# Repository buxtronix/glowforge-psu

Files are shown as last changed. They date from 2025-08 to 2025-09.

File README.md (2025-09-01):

# Documenting the Glowforge Power Supply

This repository aims to contain a collection of information on the
power supply within the Glowforge Pro.

These power supplies frequently fail, and there is little documentation
that can assist when trying to repair them.

[Scott Wiederhold](https://community.openglow.org/u/scottw514/summary) has
done a remarkable job at trying to reverse engineer the GF in order to
produce an Open Source replacement controller and his
[OpenGlow forum](http://community.openglow.org/) contains a lot of
photos, teardowns and information.

I have been trying to repair a broken power supply myself, and wanted
to combine a bunch of information from various posts, as well as what
myself and others found.

> [!TIP]
> Please contribute here if you can. Any additional or improved
> information will be greatly appreciated by many.

> [!CAUTION]
> This information involves working with lethal voltages (400-22,000 volts)
> and high power laser radiation!
> It is intended only for people who are sufficiently experienced in
> working with high voltage electronics and understand the necessary
> precautions.

> [!WARNING]
> The information contained here is provided on a "best effort" basis
> and is not guaranteed to be accurate. Consider this information to
> be a starting point where you should then use your best judgement
> and double checks before relying on anything.

## References

Some links to relevant information, mostly on OpenGlow:

 * [Teardown of power components](https://community.openglow.org/t/reverse-engineering-pr0n/242/2)
 * [High voltage troubleshooting](https://community.openglow.org/t/laser-not-firing/680/2)
 * [Testing HV output](https://community.openglow.org/t/gf-not-fire-working-process/847/2)
 * [Analysis/photos of GF boards](https://community.openglow.org/t/list-of-ics-on-the-control-board/988)
 * [OpenGlow schematic](https://community.openglow.org/t/openglow-prototype-2-schematics/255)

## Extracting the supply

The power supply is quite difficult to get out, as it wedged into a tight
corner and attached using cables with very little slack.

Ken S has made [two](https://www.youtube.com/watch?v=dVIbavUEy1M)
[videos](https://www.youtube.com/watch?v=0B0-IHG0M_s) of the removal
process which is very involved and will probably take an hour.
At one point the machine is flipped upside down - take great care
to ensure the gantry is secure as you dont want it crashing to
one side during the flip.

## Basic information.

A lot of basic teardown information can be found in
[this post](https://community.openglow.org/t/reverse-engineering-pr0n/242)
from Scott.

The power supply is a custom unit which provides several voltages
required by the machine:

 * 3.3v for logic and control board.
 * 12v for various accessories (pump, fans, motors, etc)
 * 40v for higher power components (more fans, peltier perhaps?)
 * 12-22kV for the laser tube.

It also has some control signals which communicate over the ribbon
cable. The 12v, 40v, and HV outputs are only enabled when the right
control signals are set.

It's possible to control the PSU when outside the machine, per
[this post](https://community.openglow.org/t/gf-not-fire-working-process/847/2)

## Opening the PSU

Remove the screws attaching the top lid (where the ribbon cable and HV red
wire are).

Remove the panel on the side by undoing the 4 screws holding it on.

In that panel you can access two cable bundles between the top and bottom
boards. Unplug these from the bottom board.

Remove the top cover and attached board. Take care with the red and white
wires. The red HV wire has a grommet that splits apart when the cable tie
is removed.

The top board is screwed into the lid with 8 Phillips head screws. You will
need to use a driver with a thin shaft to remove the center one as there
is not much space. Be careful not to damage or crack the core of the
flyback transformer.

## Connectors

These are the connectors on the PSU. You could create extension cables in order
to run the machine with the PSU outside of it for testing.

__Molex mini-fit jr 6-way__ is the large 6-pin connector to the daughterboard [Digikey link](https://www.digikey.com/en/products/detail/molex/0766500076/2115933)
  
__TE Connectivity Economy 2.5 4 way__ is the smaller one next to it [Digikey link](https://www.digikey.com/en/products/detail/te-connectivity-amp-connectors/1744417-4/4730270) [mating connector](https://www.digikey.com/en/products/detail/te-connectivity-amp-connectors/1969588-4/5021426)

__Molex 30-way 1mm ribbon cable__ note top on on side bottom on the other [Digikey link](https://www.digikey.com/en/products/detail/molex/0152670468/4427333)

This is the pinout of the ribbon cable:

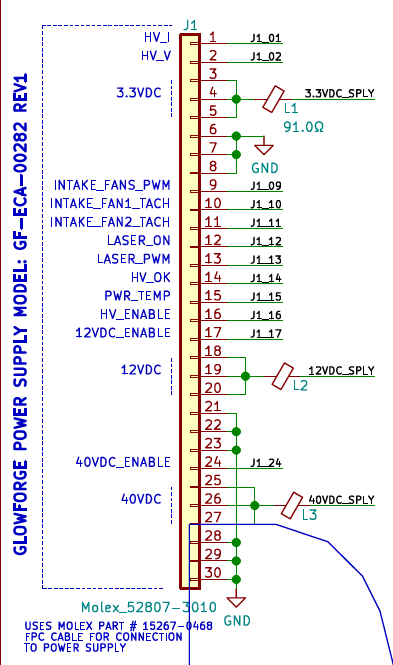
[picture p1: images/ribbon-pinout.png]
Ribbon cable pinout


## Common failure modes

### Red wire

The long red wire carries the high voltage to the laser tube. This
is a common cause of laser failures, with the insulation failing
and the power arcing through to the gantry earth.

There is loads of information online, just search for "glowforge red wire".

### Flyback transformer failure

The high voltage transformer can fail. It seems a common failure mode is
for the components in the potted section to burn out. The currently only
know fix for this is to replace the transformer from a donor unit (the
transformer is a custom unit and cannot be purchased separately).

It *might* be possible to repair the failed parts, but it is risky and
would require cutting the parts out of the potting , replacing them,
and re-potting it. A vacuum chamber would be needed at minimum to
remove air bubbles which would otherwise enable arc-over internally.

### HV supervisor failure

[TODO]

### Low voltage failures

[TODO]

## HV circuit description

TODO: Describe HV principle, operation and parts.

The driver daughterboard has some reverse engineering attempts
documented [here](hv-supervisor/)

## HV circuit troubleshooting

## Testing the supply

### Powerup testing

Using an appropriate dummy load and sending the right control signals,
the various outputs on the supply can be enabled for testing.

Scott has [a post](https://community.openglow.org/t/gf-not-fire-working-process/847/2)
covering this procedure.

Setting the various signals on the ribbon cable can be tricky. I designed a
breakout board which brings these connections into a regular header socket,
and also acts as a passthrough to the control board for verify operation
when installed.

Designs and Gerbers are [available here](breakout-pcb/).

### Flyback ring test

The secondary windings on the flyback can become shorted. This will result
in no or very weak output to the tube, and potential failure of the output
Mosfets.

It's possible to test for such a short with a ring test. A ring test works
by applying a weak square wave to a resonant circuit around the flyback core.
On a good flyback, the circuit will "ring" and oscillate with a gradual
dampening. If there is a shorted turn, this will absorb all the energy
and the ring will diminish rapidly, much like a ringing bell being touched.

This test can be easily done using just a scope, a capacitor (~0.5-2uF), and
a length of thin wire. It's not necessary to remove the flyback from the
PCB.

The diagram below shows the testing setup. It consists of:

 * A scope with a signal output, 1kHz at 1 volt (often the "cal" output)
 * A capacitor (non-polarised, ideally film) of between 0.5 and 2uF
 * 4-5 turns of insulated wire around the core. Thin, as there's not much space.
 * Connect it all in parallel - the flyback does not need to be removed from the PCB
 * Set the scope timebase to 200uS/div, and the vertical to around 2-10mV/div

A flyback with no shorted turns will look something like the left picture,
whereas if it looks more like the right picture, its almost certainly got
shorted turns and the flyback will need replacing.

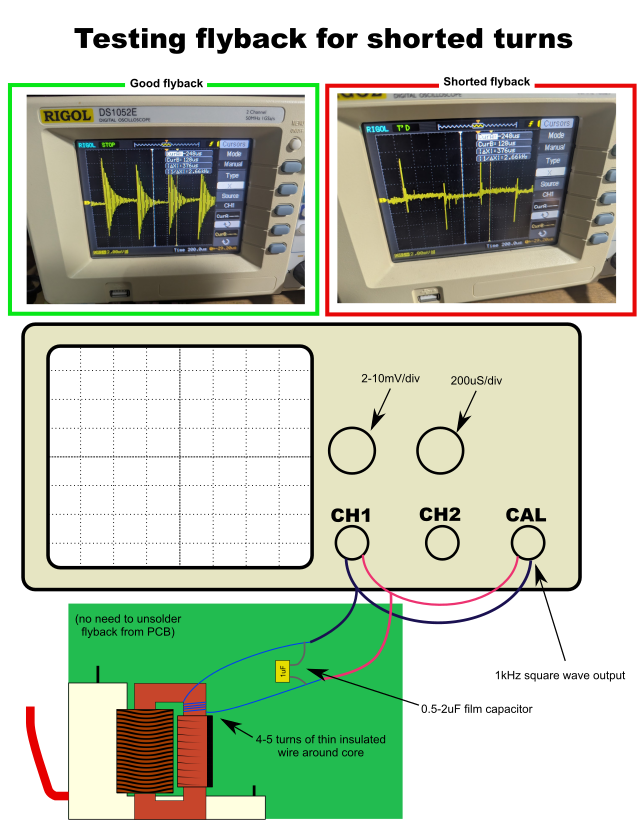
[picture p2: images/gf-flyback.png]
Flyback test setup


TODO: Add info on extending cables outside the GF machine.

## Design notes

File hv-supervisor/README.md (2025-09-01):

# HV supervisor board

This contains a work-in-progress reverse-engineered schematic of the HV supervisor
daughterboard. This is shown in
[this post](https://community.openglow.org/t/reverse-engineering-pr0n/242/2).

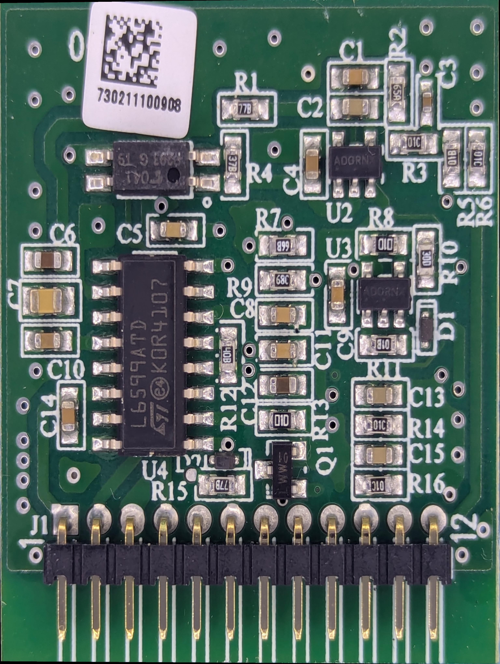
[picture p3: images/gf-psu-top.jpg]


The SOT23-5 chips are likely opamps or comparators, possibly LMC7101 or TLV7211. This is
based upon their likely function and likely pinouts. The markings don't show up on
any known database.

The main chip, an [LT6599ATD](https://www.st.com/resource/en/datasheet/l6599.pdf)
is a fairly common switchmode controller. A detailed
[reference design](https://www.mouser.com/catalog/specsheets/eval6599-90w.pdf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) is also available.

The optocoupler is likely a [TLP293](https://toshiba.semicon-storage.com/info/TLP293_datasheet_en_20191129.pdf?did=14419&prodName=TLP293).

## Pinout

This has been reverse engineered from information such as the schematic (below),
the L6599AT datasheet, 30-pin ribbon cable pinout, and various measurements.

| Pin  | Name | Description |
|---|---|---|
| 1 | OUT | This connects to the half-bridge leg, linking the two driver MOSFETs |
| 2 | HVG | The gate drive for the high side MOSFET of the half-bridge |
| 3 | GND | Ground |
| 4 | VCC | +12V supply for this board. |
| 5 | LVG | The gate drive for the low side MOSFET of the half-bridge |
| 6 |  LASER_ON  | Links to `LASER_ON` on the 30-pin ribbon. The last signal for enabling the HV |
| 7 | HV_OK | Goes low if the HV driver chip shuts off the HV. Connects to PFC_STOP of the L6599AT |
| 8 | DIS | Connects to the DIS pin of the L6599AT. Disables the chip if it is set high |
| 9 | I_SEN | Primary current sense, connects to the main sense resistors on the MOSFET low side. |
| 10 | LASER_PWM  | Links to `LASER_PWM` on the 30-pin ribbon. Used to PWM the laser for lower power cuts |
| 11 | LINE | Connects to LINE on the LA6599AT.<br/>Used for brownout detection, this senses the 60v rail is ok via a divider |
| 12 | HV_I | Tube current detection. Connects to a current sense on the HV return |

Typical signals that would be expected on these pins (also educated guesses):

| Pin  | Signal |
|---|---|
| 1 | ~60v sine wave, this is the full primary voltage.
| 2 | 12V square wave ~30KHz to drive the high side mosfet gate. |
| 3 | 0v ground |
| 4 | 12VDC as this is a stable supply voltage for this board. |
| 5 | 12V square wave ~30KHz to drive the low side mosfet gate |
| 6 | 3.3v should be applied here to turn on the HV output. |
| 7 | This should be around 1.8v (pulled high) if the chip is running |
| 8 | Should be 0v. At around 1.75v it will shutdown the chip |
| 9 | Will track the MOSFET current through the sense resistors. From 0.8v it will reduce drive, and shut off completely at 1.5v |
| 10 | PWM signal (at 3.3v) to modulate the output. Can be a DC signal for full power. 0v will disable the HV |
| 11 | Detects under and overvolt of the supply voltage. The L6599AT will shutoff with undervoltage if this is < 1.24v, and overvoltage shutoff if > 6v. This is connected via a divider to the +60v rail, also seems to be linked to `LASER_ON` on the main board. |
| 12 | Value range is unknown, but likely is proportional to the tube current measured on the HV return. Connects to an optocoupler on the STBY line of the L6599AT in similar fashion to the datasheet description, typically to regulate the output |

## Testing

The board should be independently testable, as all of the functions are
now known. Testing involves setting some voltages on various pins and
monitoring on a scope for the gate drive signals.

**The below connections may cause a failure of the driver as the correct
wiring for pin 1 is not yet known (leaving the chip OUT pin unconnected
might be problematic).** Verification TBD

| Pin  | What to connect/measure.
|---|---|
| 1 |  |
| 2 | Should be a ~30KHz square wave |
| 3 | Connect to ground |
| 4 | Connect to +12VDC |
| 5 | Should be a ~30KHz square wave out of phase with pin 2 |
| 6 | Connect this to a 3.3v source, enables the driver |
| 7 | Leave floating |
| 8 | Connect to ground. |
| 9 | Connect to ground. |
| 10 | Connect to 3.3v, PWM input |
| 11 | Connect to 3.3v to keep the brown out detector happy |
| 12 | Leave floating |

The following shows a test setup I have used with success. When measuring
the gates of both Mosfets, you will see each has a square wave out of phase
with the other. The frequency will be around 30-32KHz with a magnitude of
~24v on the high side Mosfet, and ~12v on the low side.

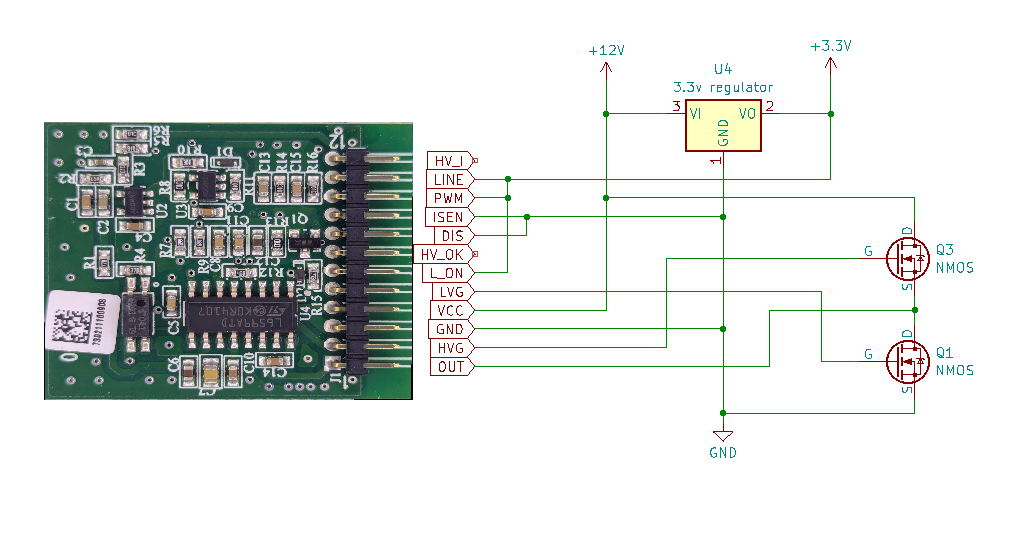
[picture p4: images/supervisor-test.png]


## Schematic

[This](glowforge-psu-hvbrd.pdf) has been reverse engineered from photos and measurements of the board. It's drawn in
Kicad and all files are here.

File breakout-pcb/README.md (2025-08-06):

# Breakout board for Glowforge power supply

A board to assist with testing and troubleshooting of a Glowforge
Pro power supply.

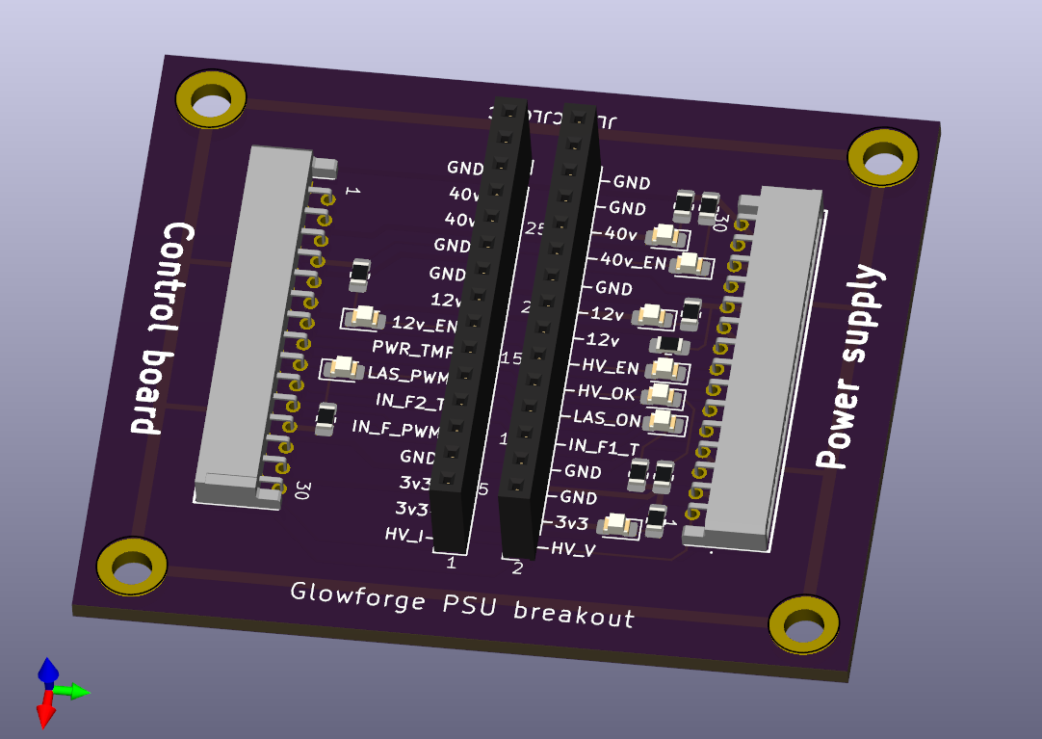
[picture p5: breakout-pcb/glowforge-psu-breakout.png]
Kicad render of breakout


Features:

- All 30 pins have passthrough and breakout to 0.1" headers.
- Can be used one-sided for testing standalone
- Can be used inline to monitor a connected supply.
- LEDs to monitor some signals

The gerbers.zip file can be uploaded to most board houses directly for
ordering. e.g for [JLCPCB](http://jlcpcb.com) upload to the 'Instant Quote'
form on their homepage, you can select the default options, order, and
have 5 boards delivered for around $USD5.

The boards will require the following additional parts:

 - 2 x Molex 52807-3010 connectors
 - 2 x 15-pin standard header sockets
 - 9 x 0805 SMD resistors
   - 1 x 8.2k
   - 1 x 2.2k
   - 7 * 270r
 - 9 x 0805 SMD LEDs

You may also need ribbon cable(s). The existing short one works to
connect to this breakout, but if you need a longer one or want to
extend, you need one with the following specs:

 - FPC cable
 - 1mm pitch
 - 30 way
 - OEM is Molex 15167 series

Note that they come in two flavours - either contacts on the same side at
both ends, or one end at the top and the other at the bottom. Between the
supply and control board as included it has the alternating one -- the
contacts on the PSU are on the bottom of the ribbon, and the contacts on
the control board are the top of the ribbon.

[Digikey link to original 50mm length](https://www.digikey.com.au/en/products/detail/molex/0151670467/3281720)

If you use this breakout as a passthrough, you will want
the variant with contacts on the same side to go to the control board.
[Digikey link to 100mm length](https://www.digikey.com.au/en/products/detail/molex/0151670471/3281724)

Longer lengths should also work and means you may be able to run the machine
with the supply outside it.

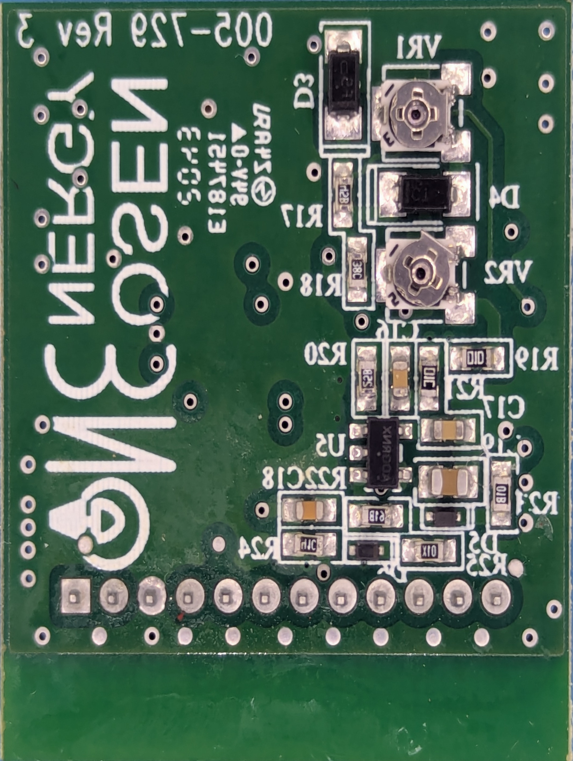
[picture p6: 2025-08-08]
images/gf-psu-bot.jpg

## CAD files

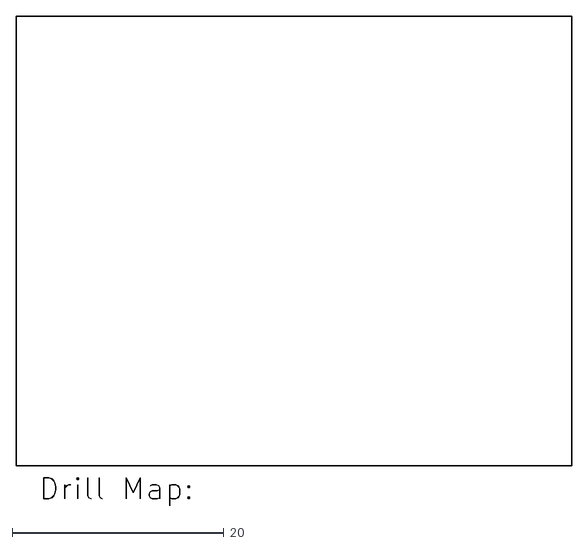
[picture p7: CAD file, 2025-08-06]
breakout-pcb/gerber/glowforge-psu-breakout-NPTH-drl_map.dxf
52.5 x 46.3

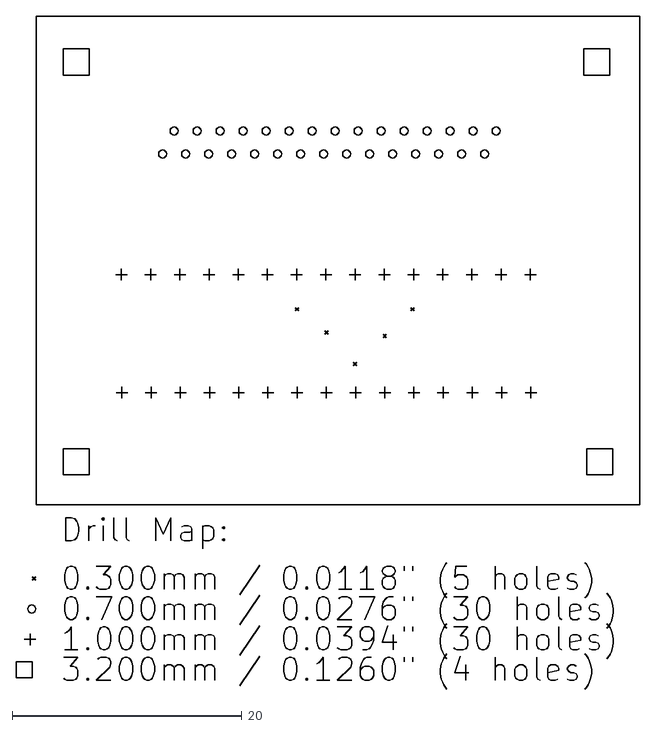
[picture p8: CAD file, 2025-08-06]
breakout-pcb/gerber/glowforge-psu-breakout-PTH-drl_map.dxf
54.2 x 58.5

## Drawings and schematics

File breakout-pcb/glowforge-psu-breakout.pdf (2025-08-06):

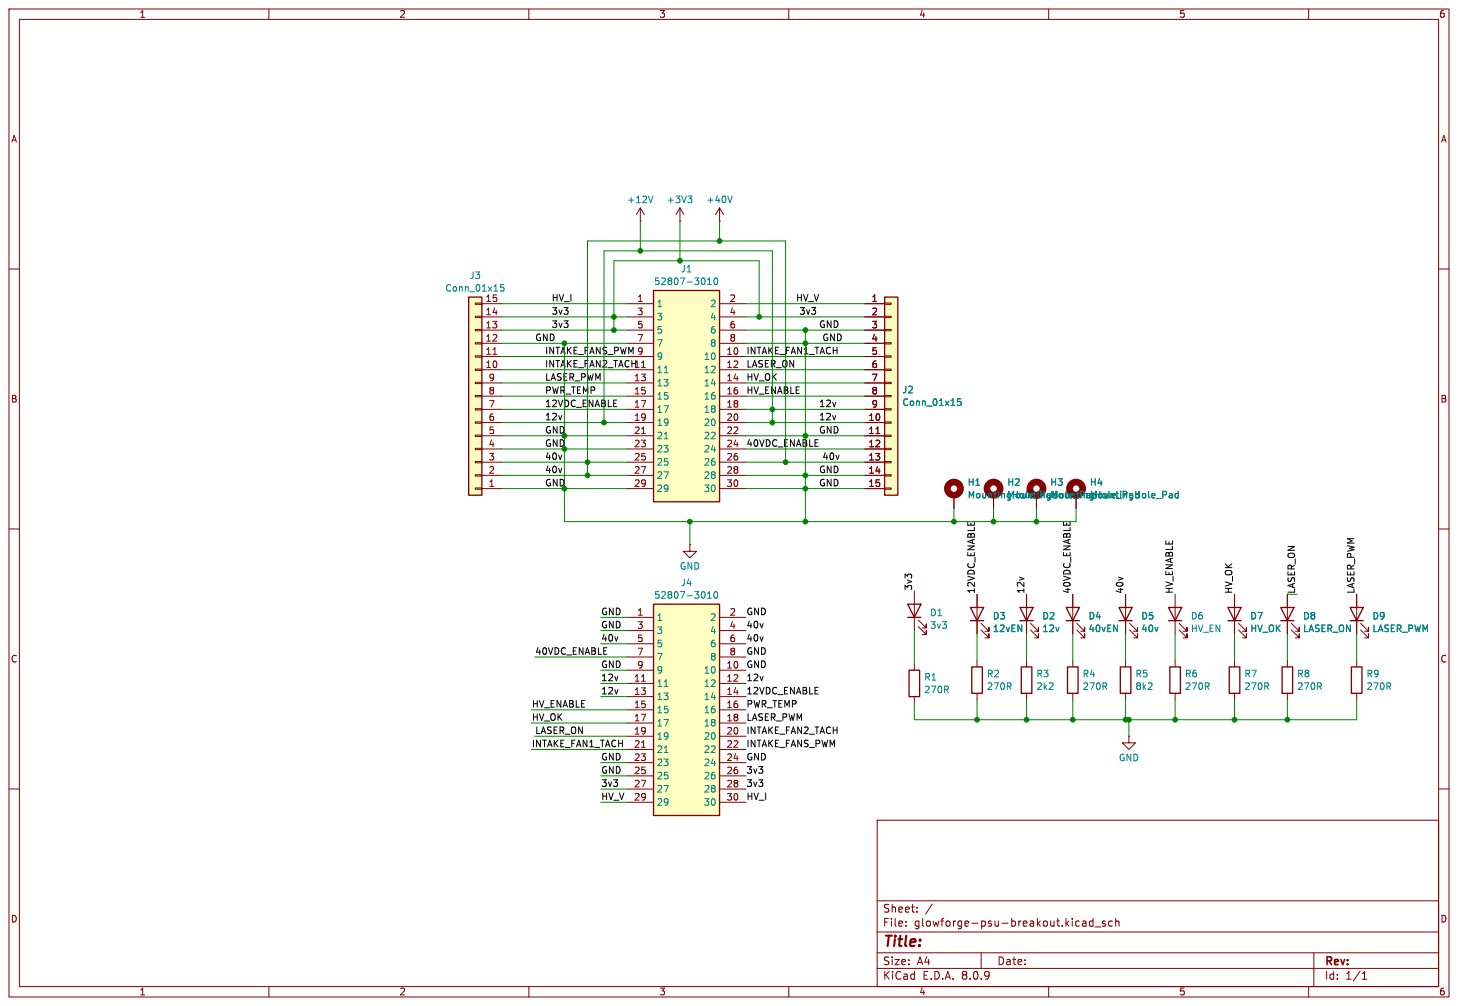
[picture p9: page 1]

Id: 1/1 Title: File: glowforge-psu-breakout.kicad_sch Sheet: /

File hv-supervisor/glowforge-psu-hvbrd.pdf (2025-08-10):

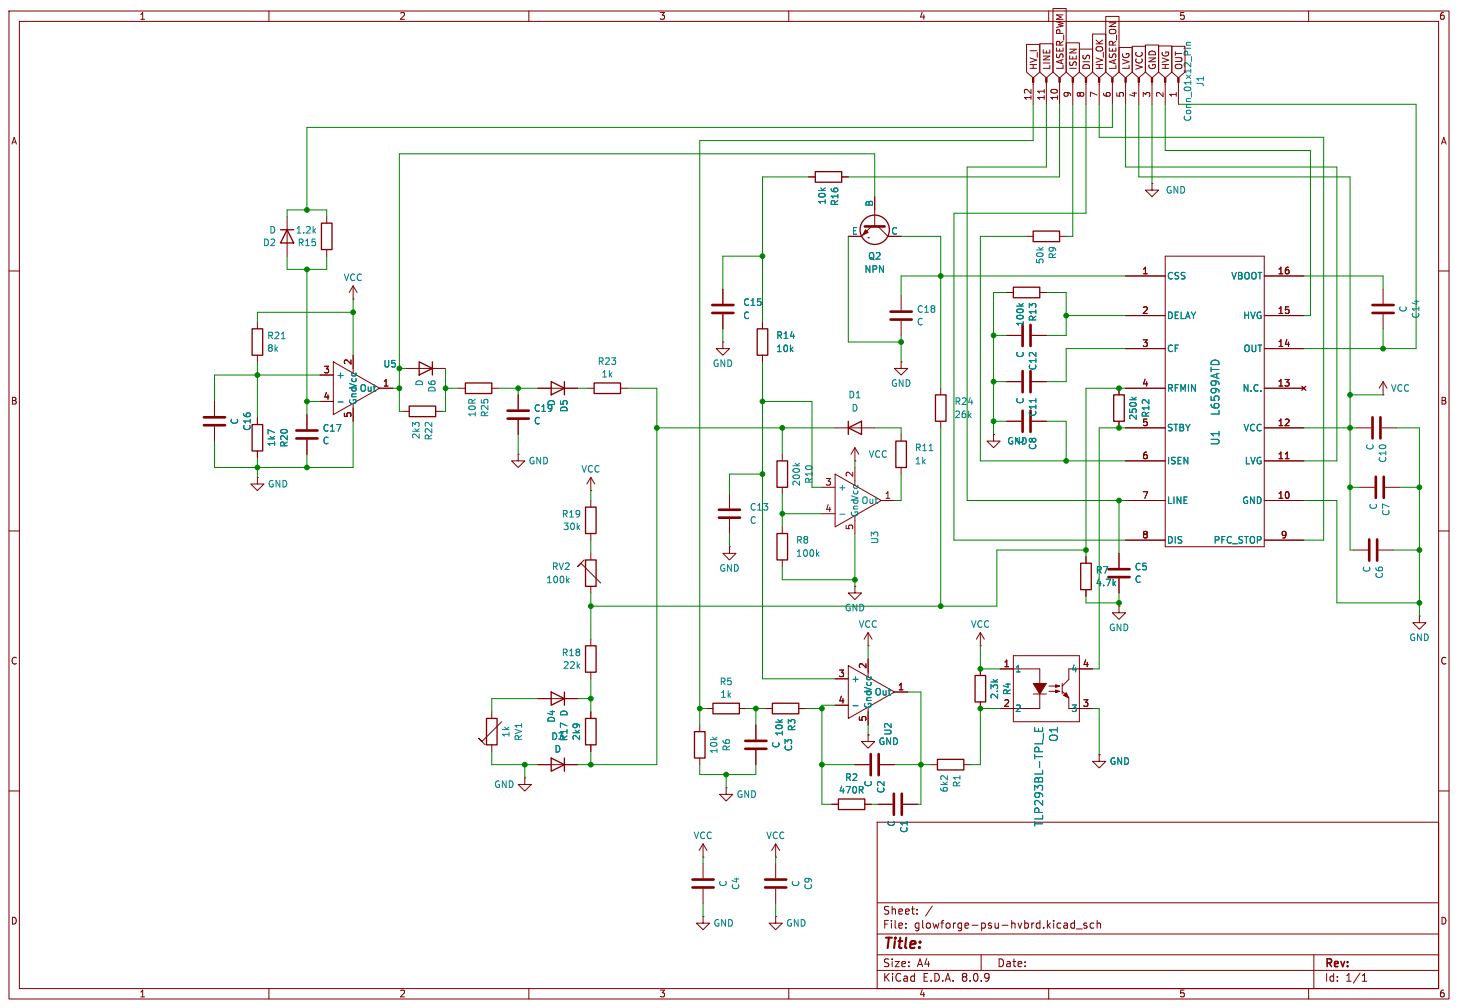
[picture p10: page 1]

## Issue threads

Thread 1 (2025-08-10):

[FAULT] No high voltage

buxtronix, 2025-08-10:
Power supply has no high voltage, however all other voltages appear correct and the machine otherwise runs fine.

The fault is not the red wire issue.

Inside the supply, the sense resistors near the flyback (R6, R7, R8) were cooked. Q5 also measured as a dead short circuit between source and drain.

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

I replaced these, however this has not resolved the fault.

When I try to fire the HV, I get the following relevant measurements:

- 60VDC on the drain of Q6 as expected.
- 0V on the gate of Q6
- 0V on the source of Q6
- 12VDC on the gate of Q5
- 0V on the source of Q5

This suggests the HV driver is not switching the mosfets, I'd expect to see a square wave of around 30KHz on the gates.

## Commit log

2025-08-05 add connector info
2025-08-06 updates and breakout
    [glowforge-psu-breakout-B_Cu.gbr, glowforge-psu-breakout-B_Mask.gbr, glowforge-psu-breakout-B_Paste.gbr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]
2025-08-08 HV driver and more
    [glowforge-psu-hvbrd.kicad_pcb, glowforge-psu-hvbrd.kicad_sch]
2025-08-08 hv driver link
2025-08-09 hv schematic update
    [glowforge-psu-hvbrd.kicad_sch]
2025-08-09 update hvdriver board
    [glowforge-psu-hvbrd.kicad_sch]
2025-08-10 label updates
    [glowforge-psu-hvbrd.kicad_sch]
2025-08-10 Update hv driver description
2025-08-10 update schematic pdf
2025-08-12 further updates
    [glowforge-psu-hvbrd.kicad_pcb, glowforge-psu-hvbrd.kicad_sch]
